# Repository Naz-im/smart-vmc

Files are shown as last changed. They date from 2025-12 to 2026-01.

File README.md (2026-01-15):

# Projet Ventilation (VMC) + App de Monitoring

## 1. Résumé du projet

Notre projet consiste à réaliser un dispositif IoT permettant d'ajuster automatiquement la ventilation (VMC) selon les conditions météo et de qualité de l’air (pluie, vent, ensoleillement, pollution, humidité si disponible) et offrant une application de monitoring et de contrôle manuel pour l'utilisateur.

## 2. Contexte et objectifs

- **Contexte** : maison connectée, qualité de l’air intérieur, efficacité énergétique
- **Objectifs principaux** :
	- Assurer une bonne qualité de l’air intérieur en adaptant le débit de ventilation aux conditions (pollution extérieure, température, humidité, vent).
	- Réduire l’humidité et évacuer l’air vicié pour prévenir moisissures et inconfort.
	- Fournir un contrôle manuel et des notifications via une application.

## 3. Périmètre

- **Matériel** :
  - moteur
  - carte ESP32
- **Logiciel**: 
		- Firmware embarqué pour l’actionneur (gestion ouverture 0–100%)
		- Application mobile pour monitoring et contrôle

## 4. Acteurs

- **Utilisateur final** : propriétaire / locataire
- **Système (embarqué)** : MCU + actionneurs
- **Application mobile** : monitoring et contrôle
- **Services tiers** : APIs météo externes

## 5. Exigences fonctionnelles 

- **01 Récupération des conditions**
	- *Description* : Le système doit pouvoir récupérer la qualité de l’air (pollution), l’humidité (si disponible), la température, la luminosité et le vent via API.
	- *Priorité* : Haute
	- *Critères d'acceptation* : Données météo reçues toutes les 10 minutes; logs des valeurs stockés localement et/ou sur cloud.

- **02 Règles d’ajustement automatique de l’ouverture**
	- *Description* : Le système ajuste automatiquement l’ouverture du clapet (et donc le débit) selon des règles configurables (ex : ouvrir davantage si pollution/CO₂/humidité > seuil, réduire sinon).
	- *Priorité* : Haute
	- *Critères d'acceptation* : Scénarios de test montrant que la règle est appliquée correctement; possibilité de forcer manuellement.

- **03 Contrôle manuel depuis l'application**
	- *Description* : L'utilisateur peut ouvrir/fermer le clapet de ventilation et régler le pourcentage d’ouverture (paliers ou valeurs) depuis l'application.
	- *Priorité* : Haute
	- *Critères d'acceptation* : Commande envoyée et état mis à jour sous 3 s; remontée d'erreur si indisponible.

- **04 Mode automatique / manuel**
	- *Description* : Basculer entre mode automatique (règles air/météo) et mode manuel.
	- *Priorité* : Moyenne
	- *Critères d'acceptation* : L'état du mode est visible et persisté.

- **05 Notifications**
	- *Description* : Recevoir notifications en cas d'événement critique (ex : surcharge/surchauffe de l’actionneur, blocage clapet, conditions extrêmes) et non critiques (ex : changement de mode, ajustement d’ouverture).
	- *Priorité* : Moyenne
	- *Critères d'acceptation* : Notification reçue sur app et log enregistrés.

- **06 Historique & Dashboard**
	- *Description* : Visualiser l'historique des états (ouvert/fermé), niveaux d’ouverture (%), mesures météo/air et interventions manuelles.
	- *Priorité* : Basse
	- *Critères d'acceptation* : Graphiques consultables.

- **07 Sécurité & protection de l’actionneur**
	- *Description* : Arrêt immédiat en cas de surintensité/surchauffe de l’actionneur; alerte en cas d’obstruction/contre‑pression détectable sur le clapet.
	- *Priorité* : Critique
	- *Critères d'acceptation* : Déclenchement de l’arrêt de sécurité sous 0.5 s lors d’une surintensité.

## 6. UI / UX

- Écrans essentiels : écran principal (ouverture ventilation: ouvert/fermé, % d’ouverture), écran historique, écran réglages (seuils air/météo), écran notifications.
- Flux : connexion --> page d'accueil --> contrôle rapide --> paramètres --> logs.

## 7. Cas d'utilisation

- En tant qu'utilisateur, je veux que l’ouverture du clapet augmente automatiquement quand la qualité de l’air est mauvaise (pollution/CO₂/humidité) ou que les conditions l’exigent.
- En tant qu'utilisateur, je veux pouvoir ouvrir/fermer le clapet et régler l’ouverture manuellement depuis l'app.

## 8. Tests & Critères d'acceptation

- Tests unitaires : firmware logique, backend endpoints.
- Tests d'intégration : envoi de télémétrie + réaction automatique.
- Tests d'acceptation utilisateur : scénarios (pluie, vent fort, obstruction) avec résultats attendus.

## Structure du projet

- `firmware/` : code embarqué pour ESP32
- `docs/` : documentation technique et utilisateur
- `Impression3DetDecoupe/` : fichiers pour impression 3D et découpe laser
- `mobile/` : code source de l'application mobile contenant principalement:
	- `android/` : code source Android pour la compilation, la génération de l'APK etc.
	- `components/` : composants réutilisables de l'application mobile
	- `hooks/` : hooks personnalisés pour la gestion de l'état et des effets secondaires
	- `App.tsx` : point d'entrée principal de l'application mobile
	- `apk/` : APK pré-généré de l'application mobile pour installation directe
	- `services/` : services pour l'application mobile (notifications, ...)
	- (Le reste des fichiers sont des configurations pour les IDE ou autres outils de développement)

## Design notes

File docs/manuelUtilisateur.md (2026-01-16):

# Manuel Utilisateur

## Installation et déploiement

Ce document décrit les procédures techniques pour flasher le microcontrôleur **ESP32** et déployer l'application mobile de monitoring.

### Flashage du Firmware sur ESP32

Le projet Le projet utilise PlatformIO pour la gestion du firmware, comme indiqué par le fichier de configuration `firmware/platformio.ini`.

#### Prérequis logiciels

- Installer [PlatformIO](https://platformio.org/install/ide?install=vscode) (extension pour VSCode recommandée).

- Avoir les drivers USB pour ESP32 installés.

#### Étapes de flashage

- Ouvrir le dossier firmware dans VSCode avec PlatformIO.
- PlatformIO détectera automatiquement le fichier `platformio.ini`.
- Connecter l'ESP32 via USB à l'ordinateur.
- Lorsque vous êtes prêt à flasher, placer vous sur le fichier `src/main.cpp` et cliquer sur l'icône "Upload" dans la barre d'outils en bas de VSCode.


- Attendre la fin du processus de compilation et de flashage. Vous verrez les logs dans la console PlatformIO.
- Pour vérifier que le firmware fonctionne, ouvrez le moniteur série en cliquant sur l'icône "Serial Monitor" dans la barre d'outils afin de voir les messages de debug.



*Note: Il est possible selon votre configuration machine que vscode n'ai pas les droits nécessaires pour accéder au port série. Dans ce cas, vous pouvez utiliser une solution immédiate mais pas très sécurisée:*

```bash
sudo chmod 666 /dev/ttyUSB0
```

*Remplacez `/dev/ttyUSB0` par le port série correspondant à votre ESP32.*

### Lancement de l'application mobile (Mode développement)

L'application mobile est développée avec React Native. Voici comment la lancer en mode développement.

#### Prérequis logiciels

- Installer [Node.js](https://nodejs.org/) version 20 ou supérieure sur votre machine.
- Installer JDK 17 pour être compatible avec gradle.
- Installer Android Studio pour émuler un appareil Android ou utiliser un appareil physique.

#### Installation des dépendances

- Ouvrir un terminal et naviguer vers le dossier `mobile`.
- Exécuter la commande suivante pour installer les dépendances :
  ```bash
  npm install
  ```

#### Lancement de l'application

Vous avez besoin de deux terminaux :

1. Dans le premier terminal, toujours dans le dossier `mobile`, lancer le serveur Metro avec la commande :
   ```bash
   npm start
   ```

2. Dans le second terminal, lancer l'application sur un émulateur ou un appareil connecté avec la commande :
   ```bash
    npm run android
    ```

*Note : Assurez-vous qu'Android Studio est lancé avec un émulateur lancé ou un téléphone Android branché avec le "Débogage USB" activé.*

L'application devrait se lancer sur l'émulateur ou l'appareil connecté. Vous pouvez maintenant interagir avec l'application mobile pour le monitoring et le contrôle de la ventilation.

#### Génération d'un APK pour distribution

Si vous souhaitez installer l'application sur un téléphone sans utiliser le mode développement (usage "client"), vous devez générer un fichier APK.

Pour des notions de praticité, un apk de l'état du projet au rendu est disponible dans le dossier `mobile/apk`

Sinon vous pouvez le générer:

1. Générer l'APK en mode release avec la commande :
   ```bash
   cd android
   ./gradlew assembleRelease
   ```
2. L'APK généré se trouvera dans le dossier `android/app/build/outputs/apk/release/`. Vous pouvez l'installer sur un appareil Android soit:
   - En le transférant via USB et en l'ouvrant sur l'appareil.
   - Avec adbr sideloading :
     ```bash
     adb install -r mobile/android/app/build/outputs/apk/release/app-release.apk
     ```

L'application devrait maintenant être installée et prête à l'emploi sur votre appareil Android.

## Utilisation de l'application

L'application mobile permet de surveiller et de contrôler le dispositif de ventilation. Voici les principales fonctionnalités :

### Première connexion

- Ouvrez l'application sur votre appareil Android.
- L'application doit tout d'abord permettre de configurer les paramètres wi-fi pour que l'ESP32 puisse se connecter à votre réseau domestique.
- Suivez les instructions à l'écran pour entrer le SSID et le mot de passe de votre réseau Wi-Fi. Vous verrer également la possibilité de configurer la latitude et la longitude pour la récupération des données météo, celle-ci sont pré-remplis selon votre position GPS si vous avez autorisé l'application à y accéder sinon par défaut sur Grenoble.

<p align="center">
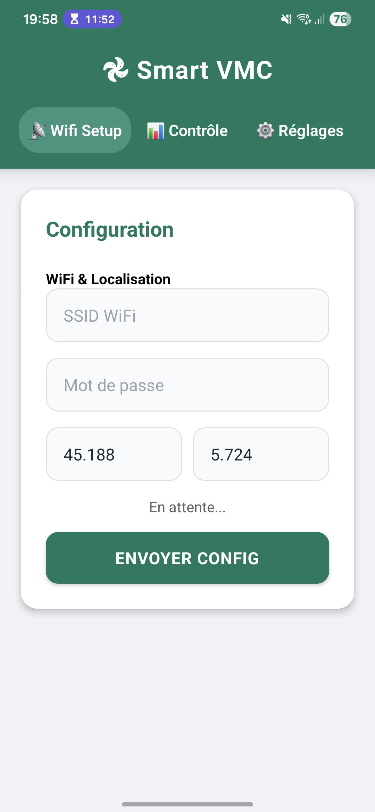
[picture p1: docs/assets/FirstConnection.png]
First Connection
    
</p>

### Dashboard principal

- Après la connexion, vous serez redirigé vers le tableau de bord principal. (Il n'est plus nécessaire de se reconnecter à chaque ouverture de l'application, les paramètres sont sauvegardés localement).
- Le tableau de bord affiche l'état actuel du clapet de ventilation (ouvert/fermé), le pourcentage d'ouverture, ainsi que les données météo et qualité de l'air en temps réel.

<p align="center">
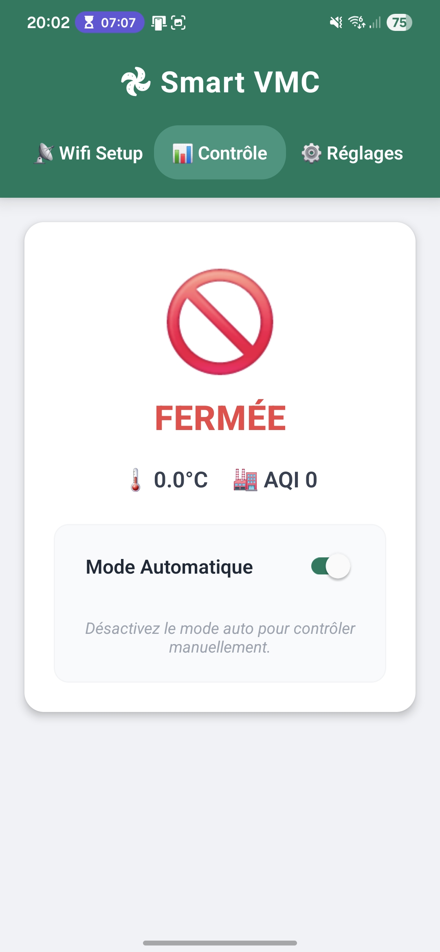
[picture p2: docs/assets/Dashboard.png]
Dashboard
    
</p>

D'ici, vous pouvez switcher entre le mode automatique et manuel, une fois en mode manuel vous pouvez régler l'ouverture du clapet via le slider ou les boutons d'ouverture/fermeture rapide.

<p align="center">
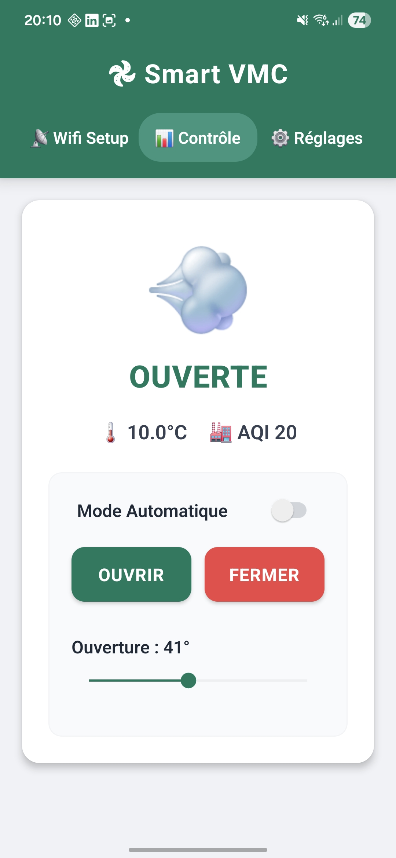
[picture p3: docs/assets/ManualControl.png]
Manual Control
    
</p>

En cas d'activation de la sécurité de blocage, un message d'alerte s'affichera:

<p align="center">
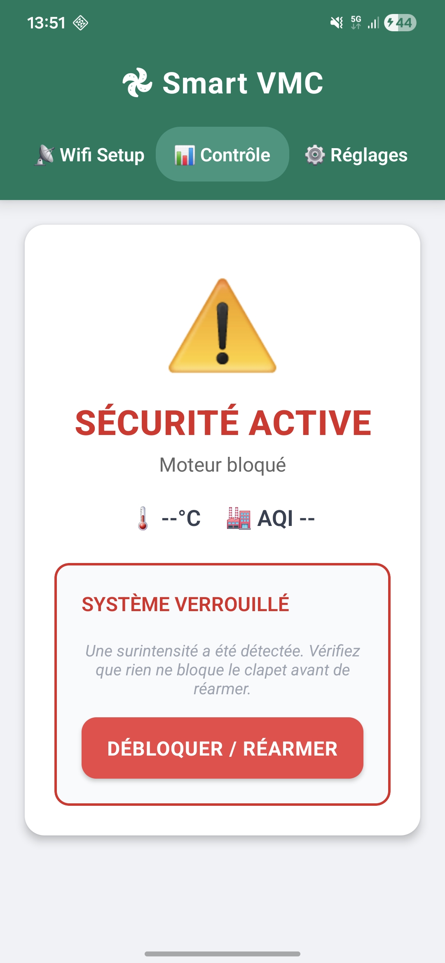
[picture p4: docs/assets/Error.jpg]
Alert
    
</p>

### Paramétrage des seuils

- Accédez à l'écran des paramètres en cliquant sur l'icône d'engrenage suivi de reglages.
- Ici, vous pouvez définir les seuils pour le mode automatique.

<p align="center">
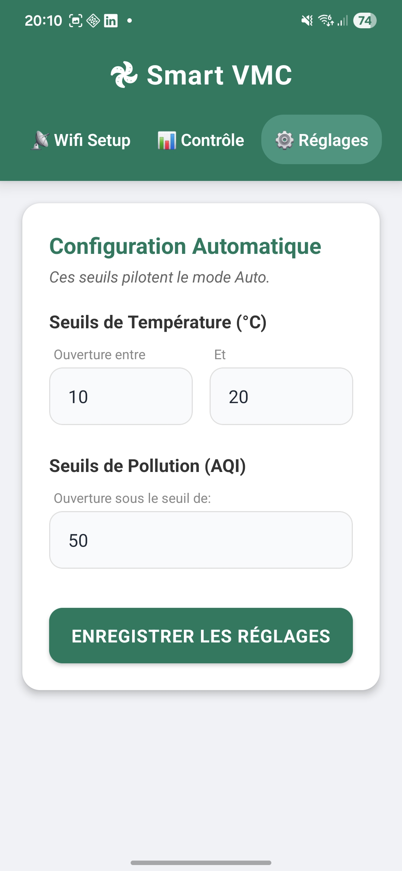
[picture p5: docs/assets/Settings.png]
Settings
    
</p>

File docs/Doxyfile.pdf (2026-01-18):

## Smart VMC

1.0

Generated on Sun Jan 18 2026 09:43:30 for Smart VMC by Doxygen 1.15.0

Sun Jan 18 2026 09:43:30

# Chapter 1

# Directory Hierarchy

## 1.1 Directories

components | | ??
dashboard | | ??
ControlPanel.tsx | | ??
SensorRow.tsx | | ??
StatusDisplay.tsx | ??
ui | ??
AppButton.tsx | ??
AppInput.tsx | ??
Card.tsx | ??
ConfigurationPanel.tsx | ??
DashboardPanel.tsx | ??
SetupPanel.tsx | ??
TabHeader.tsx | ??
dashboard | | | ??
ControlPanel.tsx | | ??
SensorRow.tsx | | ??
StatusDisplay.tsx | ??
firmware | ??
src | ??
main.hpp | | ??
hooks | | ??
useBLE.ts | ??
useWindowApi.ts | ??
mobile | ??
components | ??
dashboard | | ??
ControlPanel.tsx | | ??
SensorRow.tsx | | ??
StatusDisplay.tsx | ??
ui | ??
AppButton.tsx | ??
AppInput.tsx | ??
Card.tsx | ??
ConfigurationPanel.tsx | ??
DashboardPanel.tsx | ??
SetupPanel.tsx | ??

Generated on Sun Jan 18 2026 09:43:30 for Smart VMC by Doxygen

### 2 Directory Hierarchy

TabHeader.tsx | ??
hooks | ??
useBLE.ts | ??
useWindowApi.ts | ??
services | ??
NotificationService.ts | ??
App.tsx | | ??
services | | ??
NotificationService.ts | ??
src | | ??
main.hpp | | ??
ui | | | ??
AppButton.tsx | ??
AppInput.tsx | ??
Card.tsx | ??

# Chapter 2

# Hierarchical Index

## 2.1 Class Hierarchy

This inheritance list is sorted roughly, but not completely, alphabetically:

AppButtonProps | | | ??
BLECharacteristicCallbacks
ConfigCallbacks | ??
CardProps | | | ??
ConfigurationPanelProps | | ??
ControlPanelProps | | ??
DashboardPanelProps | | ??
NotificationService | | | ??
SensorRowProps | | ??
SetupPanelProps | | ??
StatusDisplayProps | | ??
TabHeaderProps | | | ??
TextInputProps
AppInputProps | | ??
WindowState | | ??

### 4 Hierarchical Index

# Chapter 3

# Class Index

## 3.1 Class List

Here are the classes, structs, unions and interfaces with brief descriptions:

AppButtonProps
Propriétés du bouton | ??
AppInputProps
Propriétés du champ de saisie | ??
CardProps
Propriétés du composant carte | ??
ConfigCallbacks
Traite les configurations WiFi et de localisation | ??
ConfigurationPanelProps
Propriétés du panneau de configuration | ??
ControlPanelProps
Propriétés du panneau de contrôle | ??
DashboardPanelProps
Propriétés du tableau de bord | | | ??
NotificationService
Service pour gérer les notifications locales | ??
SensorRowProps
Propriétés de la ligne de capteurs | | | ??
SetupPanelProps
Propriétés du panneau de configuration initiale | | | ??
StatusDisplayProps
Propriétés de l'affichage d'état | ??
TabHeaderProps
Propriétés de l’en-tête d’onglets | | | ??
WindowState
État de la fenêtre côté mobile | ??

### 6 Class Index

# Chapter 4

# File Index

## 4.1 File List

Here is a list of all files with brief descriptions:

firmware/src/main.hpp
Déclarations principales pour le firmware de contrôle de fenêtre VMC | | | ??
mobile/App.tsx
Composant principal de l'application mobile Smart VMC | | | ??
mobile/components/ConfigurationPanel.tsx
Panneau de configuration des seuils de température et pollution | | | ??
mobile/components/DashboardPanel.tsx
Tableau de bord affichant l’état, les capteurs et les commandes de la VMC | ??
mobile/components/SetupPanel.tsx
Panneau de configuration initiale avec saisie WiFi et localisation | | | ??
mobile/components/TabHeader.tsx
Barre d’onglets principale | ??
mobile/components/dashboard/ControlPanel.tsx
Panneau de contrôle de la VMC (mode auto, commandes manuelles, slider) | ??
mobile/components/dashboard/SensorRow.tsx
Ligne d'affichage des valeurs de capteurs (température et AQI) | ??
mobile/components/dashboard/StatusDisplay.tsx
Affichage de l'état global de la VMC (ouverte/fermée/verrouillée) | ??
mobile/components/ui/AppButton.tsx
Bouton applicatif stylé (primaire, danger, outline) avec état de chargement | ??
mobile/components/ui/AppInput.tsx
Champ de saisie stylé avec placeholder grisé | ??
mobile/components/ui/Card.tsx
Conteneur carte avec ombre et arrondis | ??
mobile/hooks/useBLE.ts
Hook React pour la communication Bluetooth avec l'ESP32 | ??
mobile/hooks/useWindowApi.ts
Hook React pour communiquer avec l'API smart-vmc | | ??
mobile/services/NotificationService.ts | | | ??

### 8 File Index

# Chapter 5

# Directory Documentation

## 5.1 mobile/components Directory Reference

Directories

- directory dashboard
- directory ui

Files

- file ConfigurationPanel.tsx

Panneau de configuration des seuils de température et pollution.
- file DashboardPanel.tsx

Tableau de bord affichant l’état, les capteurs et les commandes de la VMC.
- file SetupPanel.tsx

Panneau de configuration initiale avec saisie WiFi et localisation.
- file TabHeader.tsx

Barre d’onglets principale.

## 5.2 mobile/components/dashboard Directory Reference

Files

- file ControlPanel.tsx

Panneau de contrôle de la VMC (mode auto, commandes manuelles, slider).
- file SensorRow.tsx

Ligne d'affichage des valeurs de capteurs (température et AQI).
- file StatusDisplay.tsx

Affichage de l'état global de la VMC (ouverte/fermée/verrouillée).

## 5.3 firmware Directory Reference

Directories

- directory src

### 10 Directory Documentation

## 5.4 mobile/hooks Directory Reference

Files

- file useBLE.ts

Hook React pour la communication Bluetooth avec l'ESP32.
- file useWindowApi.ts

Hook React pour communiquer avec l'API smart-vmc.

## 5.5 mobile Directory Reference

Directories

- directory components
- directory hooks
- directory services

Files

- file App.tsx

Composant principal de l'application mobile Smart VMC.

## 5.6 mobile/services Directory Reference

Files

- file NotificationService.ts

## 5.7 firmware/src Directory Reference

Files

- file main.hpp

Déclarations principales pour le firmware de contrôle de fenêtre VMC.

## 5.8 mobile/components/ui Directory Reference

Files

- file AppButton.tsx

Bouton applicatif stylé (primaire, danger, outline) avec état de chargement.
- file AppInput.tsx

Champ de saisie stylé avec placeholder grisé
- file Card.tsx

Conteneur carte avec ombre et arrondis.

# Chapter 6

# Class Documentation

## 6.1 AppButtonProps Interface Reference

Propriétés du bouton.

### 6.1.1 Detailed Description

Propriétés du bouton.

The documentation for this interface was generated from the following file:

- mobile/components/ui/AppButton.tsx

## 6.2 AppInputProps Interface Reference

Propriétés du champ de saisie.

Inheritance diagram for AppInputProps:

AppInputProps

TextInputProps

### 6.2.1 Detailed Description

Propriétés du champ de saisie.

The documentation for this interface was generated from the following file:

- mobile/components/ui/AppInput.tsx

### 12 Class Documentation

## 6.3 CardProps Interface Reference

Propriétés du composant carte.

### 6.3.1 Detailed Description

Propriétés du composant carte.

The documentation for this interface was generated from the following file:

- mobile/components/ui/Card.tsx

## 6.4 ConfigCallbacks Class Reference

Traite les configurations WiFi et de localisation.

#include <main.hpp>

Inheritance diagram for ConfigCallbacks:

ConfigCallbacks

BLECharacteristicCallbacks

### 6.4.1 Detailed Description

Traite les configurations WiFi et de localisation.

The documentation for this class was generated from the following file:

- firmware/src/main.hpp

## 6.5 ConfigurationPanelProps Interface Reference

Propriétés du panneau de configuration.

### 6.5.1 Detailed Description

Propriétés du panneau de configuration.

The documentation for this interface was generated from the following file:

- mobile/components/ConfigurationPanel.tsx

6.6 ControlPanelProps Interface Reference | 13

## 6.6 ControlPanelProps Interface Reference

Propriétés du panneau de contrôle.

### 6.6.1 Detailed Description

Propriétés du panneau de contrôle.

The documentation for this interface was generated from the following file:

- mobile/components/dashboard/ControlPanel.tsx

## 6.7 DashboardPanelProps Interface Reference

Propriétés du tableau de bord.

### 6.7.1 Detailed Description

Propriétés du tableau de bord.

The documentation for this interface was generated from the following file:

- mobile/components/DashboardPanel.tsx

## 6.8 NotificationService Class Reference

Service pour gérer les notifications locales.

Public Member Functions

- async requestPermission ()

@function requestPermission
- async createChannel ()

@function createChannel
- async displayNotification (title:string, body:string)

@function displayNotification

### 6.8.1 Detailed Description

Service pour gérer les notifications locales.

Ce service utilise la bibliothèque Notifee pour :

- Demander la permission d'envoyer des notifications
- Créer un canal de notification pour les alertes VMC
- Afficher des notifications locales avec un titre et un corps

### 14 Class Documentation

### 6.8.2 Member Function Documentation

### 6.8.2.1 createChannel()

async NotificationService::createChannel () [inline]

@function createChannel

Crée un canal de notification pour les alertes VMC

Returns

{Promise<string>} L'ID du canal créé

### 6.8.2.2 displayNotification()

async NotificationService::displayNotification (

title:string,

body:string) [inline]

@function displayNotification

Affiche une notification locale avec le titre et le corps spécifiés

Parameters

{string} | title - Le titre de la notification
{string} | body - Le corps de la notification

### 6.8.2.3 requestPermission()

async NotificationService::requestPermission () [inline]

@function requestPermission

Demande la permission d'envoyer des notifications

Returns

{Promise<boolean>} Vrai si la permission est accordée, sinon faux

The documentation for this class was generated from the following file:

- mobile/services/NotificationService.ts

## 6.9 SensorRowProps Interface Reference

Propriétés de la ligne de capteurs.

6.10 SetupPanelProps Interface Reference | 15

### 6.9.1 Detailed Description

Propriétés de la ligne de capteurs.

The documentation for this interface was generated from the following file:

- mobile/components/dashboard/SensorRow.tsx

## 6.10 SetupPanelProps Interface Reference

Propriétés du panneau de configuration initiale.

### 6.10.1 Detailed Description

Propriétés du panneau de configuration initiale.

The documentation for this interface was generated from the following file:

- mobile/components/SetupPanel.tsx

## 6.11 StatusDisplayProps Interface Reference

Propriétés de l'affichage d'état.

### 6.11.1 Detailed Description

Propriétés de l'affichage d'état.

The documentation for this interface was generated from the following file:

- mobile/components/dashboard/StatusDisplay.tsx

## 6.12 TabHeaderProps Interface Reference

Propriétés de l’en-tête d’onglets.

### 6.12.1 Detailed Description

Propriétés de l’en-tête d’onglets.

The documentation for this interface was generated from the following file:

- mobile/components/TabHeader.tsx

### 16 Class Documentation

## 6.13 WindowState Interface Reference

État de la fenêtre côté mobile.

### 6.13.1 Detailed Description

État de la fenêtre côté mobile.

The documentation for this interface was generated from the following file:

- mobile/hooks/useWindowApi.ts

# Chapter 7

# File Documentation

## 7.1 firmware/src/main.hpp File Reference

Déclarations principales pour le firmware de contrôle de fenêtre VMC.

#include <Arduino.h>

#include <WiFi.h>

#include <HTTPClient.h>

#include <WebServer.h>

#include <ArduinoJson.h>

#include <ESP32Servo.h>

#include <NimBLEDevice.h>

#include <Preferences.h>

Classes

- class ConfigCallbacks

Traite les configurations WiFi et de localisation.

Macros

- #define SERVO_PIN 13

Variable pin du servomoteur.
- #define CURRENT_SENSOR_PIN 34

Variable pin du capteur de courant.
- #define MAX_CURRENT_THRESHOLD 2500

Seuil de courant maximal en mA.
- #define SERVICE_UUID "4fafc201-1fb5-459e-8fcc-c5c9c331914b"

UUIDs pour le service et les caractéristiques BLE.
- #define CHAR_CONFIG_UUID "beb5483e-36e1-4688-b7f5-ea07361b26a8"

UUID de la caractéristique de configuration (WiFi, localisation).
- #define CHAR_IP_UUID "12345678-1234-1234-1234-1234567890ab"

UUID de la caractéristique d'adresse IP.

### 18 File Documentation

Functions

- bool checkSafety ()

Vérifie l'état de sécurité du système.
- void setVMC (int angle)

Commande le servomoteur à un angle spécifique.
- void handleStatus ()

Gestionnaire HTTP GET /api/window/status.
- void handleControl ()

Gestionnaire HTTP POST /api/window/control.
- void setup ()

Initialisation de la connexion (WiFi, BLE, serveur).
- void loop ()

Boucle d'exécution principale.

Variables

- Servo windowServo

Objet servomoteur pour contrôler l'ouverture de la fenêtre.
- Preferences preferences

Objet Preferences pour stocker la configuration persistante.
- WebServer server

Objet WebServer pour gérer les requêtes HTTP.
- BLECharacteristic ∗ pIpChar

Caractéristique BLE pour l'adresse IP.
- String wifi_ssid

SSID WiFi.
- String wifi_pass

Mot de passe WiFi.
- float latitude

Variable de configuration de localisation.
- float longitude

Variable de configuration de localisation.
- float tempMax

Variables de configuration de la température maximum.
- float tempMin

Variables de configuration de la température minimum.
- int aqiMax

Variables de configuration de la qualité de l'air maximum.
- bool isOpen

Indique si la ventilation est ouverte.
- bool autoMode

Indique si le mode automatique est activé
- int targetAngle

Angle cible pour le servomoteur.
- bool safetyLockout

Indique si le verrouillage de sécurité est activé
- int lastCurrentReading

Dernière lecture du courant en mA.
- int currentAngle

7.1 firmware/src/main.hpp File Reference | 19

Angle actuel du servomoteur.
- float lastTemp

Dernière température lue.
- int lastAQI

Dernière qualité de l'air lue.
- unsigned long lastWeatherCheck

Timestamp de la dernière vérification météo.
- bool shouldRestart

Indique si un redémarrage est nécessaire.

### 7.1.1 Detailed Description

Déclarations principales pour le firmware de contrôle de fenêtre VMC.

### 7.1.2 Macro Definition Documentation

### 7.1.2.1 CHAR_CONFIG_UUID

#define CHAR_CONFIG_UUID "beb5483e-36e1-4688-b7f5-ea07361b26a8"

UUID de la caractéristique de configuration (WiFi, localisation).

### 7.1.2.2 CHAR_IP_UUID

#define CHAR_IP_UUID "12345678-1234-1234-1234-1234567890ab"

UUID de la caractéristique d'adresse IP.

### 7.1.2.3 CURRENT_SENSOR_PIN

#define CURRENT_SENSOR_PIN 34

Variable pin du capteur de courant.

### 7.1.2.4 MAX_CURRENT_THRESHOLD

#define MAX_CURRENT_THRESHOLD 2500

Seuil de courant maximal en mA.

### 7.1.2.5 SERVICE_UUID

#define SERVICE_UUID "4fafc201-1fb5-459e-8fcc-c5c9c331914b"

UUIDs pour le service et les caractéristiques BLE.

### 20 File Documentation

### 7.1.2.6 SERVO_PIN

#define SERVO_PIN 13

Variable pin du servomoteur.

### 7.1.3 Function Documentation

### 7.1.3.1 checkSafety()

bool checkSafety ()

Vérifie l'état de sécurité du système.

Lit le capteur de courant et vérifie s'il dépasse le seuil

Returns

true si sécurisé, false si surintensité détectée

### 7.1.3.2 handleControl()

void handleControl ()

Gestionnaire HTTP POST /api/window/control.

Reçoit les commandes pour contrôler la fenêtre

### 7.1.3.3 handleStatus()

void handleStatus ()

Gestionnaire HTTP GET /api/window/status.

Retourne l'état complet du système en JSON

### 7.1.3.4 loop()

void loop ()

Boucle d'exécution principale.

Gère les requêtes HTTP, la météo et les redémarrages

### 7.1.3.5 setup()

void setup ()

Initialisation de la connexion (WiFi, BLE, serveur).

### 7.1.3.6 setVMC()

void setVMC (

int angle)

Commande le servomoteur à un angle spécifique.

Parameters

7.1 firmware/src/main.hpp File Reference | 21
angle | Angle cible en degrés (0-90)

Vérifie la sécurité, contraint l'angle et met à jour l'état

### 7.1.4 Variable Documentation

### 7.1.4.1 aqiMax

int aqiMax [extern]

Variables de configuration de la qualité de l'air maximum.

### 7.1.4.2 autoMode

bool autoMode [extern]

Indique si le mode automatique est activé

### 7.1.4.3 currentAngle

int currentAngle [extern]

Angle actuel du servomoteur.

### 7.1.4.4 isOpen

bool isOpen [extern]

Indique si la ventilation est ouverte.

### 7.1.4.5 lastAQI

int lastAQI [extern]

Dernière qualité de l'air lue.

### 7.1.4.6 lastCurrentReading

int lastCurrentReading [extern]

Dernière lecture du courant en mA.

### 22 File Documentation

### 7.1.4.7 lastTemp

float lastTemp [extern]

Dernière température lue.

### 7.1.4.8 lastWeatherCheck

unsigned long lastWeatherCheck [extern]

Timestamp de la dernière vérification météo.

### 7.1.4.9 latitude

float latitude [extern]

Variable de configuration de localisation.

### 7.1.4.10 longitude

float longitude [extern]

Variable de configuration de localisation.

### 7.1.4.11 pIpChar

BLECharacteristic∗ pIpChar [extern]

Caractéristique BLE pour l'adresse IP.

### 7.1.4.12 preferences

Preferences preferences [extern]

Objet Preferences pour stocker la configuration persistante.

### 7.1.4.13 safetyLockout

bool safetyLockout [extern]

Indique si le verrouillage de sécurité est activé

### 7.1.4.14 server

WebServer server [extern]

Objet WebServer pour gérer les requêtes HTTP.

7.1 firmware/src/main.hpp File Reference | 23

### 7.1.4.15 shouldRestart

bool shouldRestart [extern]

Indique si un redémarrage est nécessaire.

### 7.1.4.16 targetAngle

int targetAngle [extern]

Angle cible pour le servomoteur.

### 7.1.4.17 tempMax

float tempMax [extern]

Variables de configuration de la température maximum.

### 7.1.4.18 tempMin

float tempMin [extern]

Variables de configuration de la température minimum.

### 7.1.4.19 wifi_pass

String wifi_pass [extern]

Mot de passe WiFi.

### 7.1.4.20 wifi_ssid

String wifi_ssid [extern]

SSID WiFi.

### 7.1.4.21 windowServo

Servo windowServo [extern]

Objet servomoteur pour contrôler l'ouverture de la fenêtre.

### 24 File Documentation

## 7.2 main.hpp

Go to the documentation of this file.

00001 #ifndef MAIN_HPP
00002 #define MAIN_HPP
00003
00004 #include <Arduino.h> 00005 #include <WiFi.h>
00006 #include <HTTPClient.h> 00007 #include <WebServer.h> 00008 #include <ArduinoJson.h> 00009 #include <ESP32Servo.h> 00010 #include <NimBLEDevice.h> 00011 #include <Preferences.h> 00012
00016
00020 #define SERVO_PIN 13
00024 #define CURRENT_SENSOR_PIN 34
00028 #define MAX_CURRENT_THRESHOLD 2500
00032 #define SERVICE_UUID "4fafc201-1fb5-459e-8fcc-c5c9c331914b" 00036 #define CHAR_CONFIG_UUID "beb5483e-36e1-4688-b7f5-ea07361b26a8" 00040 #define CHAR_IP_UUID "12345678-1234-1234-1234-1234567890ab" 00041
00045 extern Servo windowServo;
00046
00050 extern Preferences preferences; 00051
00055 extern WebServer server;
00056
00060 extern BLECharacteristic *pIpChar; 00061
00065 extern String wifi_ssid;
00069 extern String wifi_pass;
00070
00074 extern float latitude; 00078 extern float longitude; 00082 extern float tempMax; 00086 extern float tempMin; 00090 extern int aqiMax;
00091
00095 extern bool isOpen;
00096
00100 extern bool autoMode;
00104 extern int targetAngle;
00108 extern bool safetyLockout; 00112 extern int lastCurrentReading; 00116 extern int currentAngle;
00120 extern float lastTemp;
00124 extern int lastAQI;
00128 extern unsigned long lastWeatherCheck; 00132 extern bool shouldRestart;
00133
00139 bool checkSafety();
00140
00146 void setVMC(int angle); 00147
00152 void handleStatus(); 00153
00158 void handleControl(); 00159
00163 void setup();
00168 void loop();
00169
00171
00176 class ConfigCallbacks : public BLECharacteristicCallbacks {
00181 | void onWrite(BLECharacteristic *pCharacteristic);
00182 };
00183
00184 #endif // MAIN_HPP

## 7.3 mobile/App.tsx File Reference

Composant principal de l'application mobile Smart VMC.

7.3 mobile/App.tsx File Reference | 25

Variables

- import React
- import import { SafeAreaView, ScrollView, StatusBar, StyleSheet, Alert, ActivityIndicator, View, Text } from 'react-native'
- import AsyncStorage from react native async storage async storage
- import TabHeader from components TabHeader
- import SetupPanel from components SetupPanel
- import DashboardPanel from components DashboardPanel
- import ConfigurationPanel from components ConfigurationPanel
- function App() export default App

@function App

### 7.3.1 Detailed Description

Composant principal de l'application mobile Smart VMC.

Gère la navigation entre les onglets (Setup, Dashboard, Configuration) et la communication avec l'ESP32 via BLE et API HTTP

### 7.3.2 Variable Documentation

### 7.3.2.1 App

function App () export default App ()

@function App

Composant racine de l'application Smart VMC

Gère :

- La navigation entre 3 onglets (Setup, Dashboard, Configuration)
- La connexion BLE à l'ESP32
- La communication avec l'API REST
- Le stockage persistant de l'adresse IP du serveur

Returns

{React.JSX.Element} Interface utilisateur complète

### 7.3.2.2 ConfigurationPanel

export default ConfigurationPanel

### 26 File Documentation

### 7.3.2.3 DashboardPanel

export default DashboardPanel

### 7.3.2.4 import

import { SafeAreaView, ScrollView, StatusBar, StyleSheet, Alert, ActivityIndicator, View, Text

} from 'react-native'

### 7.3.2.5 React

import React

### 7.3.2.6 SetupPanel

export default SetupPanel

### 7.3.2.7 storage

import AsyncStorage from react native async storage async storage

### 7.3.2.8 TabHeader

export default TabHeader

## 7.4 mobile/components/ConfigurationPanel.tsx File Reference

Panneau de configuration des seuils de température et pollution.

Variables

- import React
- import import { View, Text, StyleSheet, Alert } from 'react-native'
- onUpdateThresholds __pad0__
- onUpdateThresholds tMin
- onUpdateThresholds aqiMax

Variables de configuration de la qualité de l'air maximum.
- isLoading __pad1__
- const ConfigurationPanel

@function ConfigurationPanel
- const onUpdateThresholds
- const isLoading
- const styles

7.4 mobile/components/ConfigurationPanel.tsx File Reference | 27

### 7.4.1 Detailed Description

Panneau de configuration des seuils de température et pollution.

### 7.4.2 Variable Documentation

### 7.4.2.1 __pad0__

onUpdateThresholds __pad0__

### 7.4.2.2 __pad1__

isLoading __pad1__

### 7.4.2.3 aqiMax

onUpdateThresholds aqiMax

Variables de configuration de la qualité de l'air maximum.

### 7.4.2.4 ConfigurationPanel

export default ConfigurationPanel

@function ConfigurationPanel

Formulaire de configuration des seuils (température, AQI) pour le mode Auto

Parameters

{ConfigurationPanelProps} props - Propriétés du composant

Returns

{React.JSX.Element} Carte de configuration

### 7.4.2.5 import

import { View, Text, StyleSheet, Alert } from 'react-native'

### 7.4.2.6 isLoading

const isLoading

### 28 File Documentation

### 7.4.2.7 onUpdateThresholds

const onUpdateThresholds

### 7.4.2.8 React

import React

### 7.4.2.9 styles

const styles

### 7.4.2.10 tMin

onUpdateThresholds tMin

## 7.5 mobile/components/dashboard/ControlPanel.tsx File Reference

Panneau de contrôle de la VMC (mode auto, commandes manuelles, slider).

Variables

- import React from react
- import { View, Text, Switch, StyleSheet } from 'react-native'
- import Slider from react native community slider
- isLocked __pad0__
- targetAngle __pad1__
- onToggleAuto __pad2__
- onCommand __pad3__
- onAngleChange __pad4__
- onResetSafety __pad5__
- export const ControlPanel

@function ControlPanel
- export const isLocked
- export const targetAngle

Angle cible pour le servomoteur.
- export const onToggleAuto
- export const onCommand
- export const onAngleChange
- export const onResetSafety
- const styles

### 7.5.1 Detailed Description

Panneau de contrôle de la VMC (mode auto, commandes manuelles, slider).

7.5 mobile/components/dashboard/ControlPanel.tsx File Reference | 29

### 7.5.2 Variable Documentation

### 7.5.2.1 __pad0__

isLocked __pad0__

### 7.5.2.2 __pad1__

targetAngle __pad1__

### 7.5.2.3 __pad2__

onToggleAuto __pad2__

### 7.5.2.4 __pad3__

onCommand __pad3__

### 7.5.2.5 __pad4__

onAngleChange __pad4__

### 7.5.2.6 __pad5__

onResetSafety __pad5__

### 7.5.2.7 ControlPanel

export const ControlPanel

@function ControlPanel

Panneau de contrôle principal de la VMC

Parameters

{ControlPanelProps} props - Propriétés du composant

Returns

{React.JSX.Element} Panneau de contrôle

Affiche deux modes :

- Mode verrouillé : Bouton de réarmement sécurité
- Mode normal : Switch auto/manuel, boutons ouvrir/fermer, slider d'angle

### 30 File Documentation

### 7.5.2.8 import

import { View, Text, Switch, StyleSheet } from 'react-native'

### 7.5.2.9 isLocked

export const isLocked

### 7.5.2.10 onAngleChange

export const onAngleChange

### 7.5.2.11 onCommand

export const onCommand

### 7.5.2.12 onResetSafety

export const onResetSafety

### 7.5.2.13 onToggleAuto

export const onToggleAuto

### 7.5.2.14 react

import React from react

### 7.5.2.15 slider

import Slider from react native community slider

### 7.5.2.16 styles

const styles

### 7.5.2.17 targetAngle

export const targetAngle

Angle cible pour le servomoteur.

7.6 mobile/components/dashboard/SensorRow.tsx File Reference | 31

## 7.6 mobile/components/dashboard/SensorRow.tsx File Reference

Ligne d'affichage des valeurs de capteurs (température et AQI).

Variables

- import React from react
- import { View, Text, StyleSheet } from 'react-native'
- aqi __pad0__
- export const SensorRow

@function SensorRow
- export const aqi
- const styles

### 7.6.1 Detailed Description

Ligne d'affichage des valeurs de capteurs (température et AQI).

### 7.6.2 Variable Documentation

### 7.6.2.1 __pad0__

aqi __pad0__

### 7.6.2.2 aqi

export const aqi

Initial value:

=> {
return (
<View style={styles.row}>
<Text style={styles.value}> {temp !== undefined && temp !== null ? temp.toFixed(1) : ’--’}°C</Text> <Text style={styles.value}> AQI {aqi ?? ’--’}</Text>
</View>
);
}

### 7.6.2.3 import

import { View, Text, StyleSheet } from 'react-native'

### 7.6.2.4 react

import React from react

### 7.6.2.5 SensorRow

export const SensorRow

@function SensorRow

Affiche la température et l'AQI sous forme de badges

Parameters

### 32 File Documentation

{SensorRowProps} props - Propriétés du composant

Returns

{React.JSX.Element} Ligne de capteurs

### 7.6.2.6 styles

const styles

Initial value:

= StyleSheet.create({
row: {
flexDirection: ’row’,
justifyContent: ’center’,
gap: 20,
marginBottom: 25,
},
value: {
fontSize: 18,
fontWeight: ’600’,
color: ’#374151’,
},
})

## 7.7 mobile/components/dashboard/StatusDisplay.tsx File Reference

Affichage de l'état global de la VMC (ouverte/fermée/verrouillée).

Variables

- import React from react
- import { View, Text, StyleSheet } from 'react-native'
- isLocked __pad0__
- export const StatusDisplay

@function StatusDisplay
- export const isLocked
- const styles

### 7.7.1 Detailed Description

Affichage de l'état global de la VMC (ouverte/fermée/verrouillée).

### 7.7.2 Variable Documentation

### 7.7.2.1 __pad0__

isLocked __pad0__

7.7 mobile/components/dashboard/StatusDisplay.tsx File Reference | 33

### 7.7.2.2 import

import { View, Text, StyleSheet } from 'react-native'

### 7.7.2.3 isLocked

export const isLocked

Initial value:

=> {

if (isLocked) {
return (
<View style={styles.container}>
<Text style={styles.emoji}></Text>
<Text style={[styles.text, { color: ’#DC2626’ }]}> SÉCURITÉ ACTIVE
</Text>
<Text style={styles.subtext}>Moteur bloqué</Text> </View>
);
}

return (
<View style={styles.container}> <Text style={styles.emoji}> {isOpen ? ’’ : ’’}
</Text>
<Text style={[
styles.text,
{ color: isOpen ? ’#007A5E’ : ’#EF4444’ } ]}>
{isOpen ? ’OUVERTE’ : ’FERMÉE’}
</Text>
</View>
);
}

### 7.7.2.4 react

import React from react

### 7.7.2.5 StatusDisplay

export const StatusDisplay

@function StatusDisplay

Affiche l'état visuel de la VMC avec emoji et texte coloré

Parameters

{StatusDisplayProps} props - Propriétés du composant

Returns

{React.JSX.Element} Vue d'état

### 34 File Documentation

### 7.7.2.6 styles

const styles

Initial value:

= StyleSheet.create({
container: {
alignItems: ’center’,
marginBottom: 20,
},
emoji: {
fontSize: 80,
marginBottom: 10,
},
text: {
fontSize: 28,
fontWeight: ’800’,
letterSpacing: 0.5,
textAlign: ’center’,
},
subtext: {
fontSize: 16,
color: ’#666’,
marginTop: 5,
}
})

## 7.8 mobile/components/DashboardPanel.tsx File Reference

Tableau de bord affichant l’état, les capteurs et les commandes de la VMC.

Variables

- import React
- import import { StyleSheet, View } from 'react-native'
- import NotificationService from services NotificationService
- onToggleAuto __pad0__
- onCommand __pad1__
- onAngleChange __pad2__
- onResetSafety __pad3__
- const DashboardPanel

@function DashboardPanel
- const onToggleAuto
- const onCommand
- const onAngleChange
- const onResetSafety
- const styles

### 7.8.1 Detailed Description

Tableau de bord affichant l’état, les capteurs et les commandes de la VMC.

### 7.8.2 Variable Documentation

### 7.8.2.1 __pad0__

onToggleAuto __pad0__

7.8 mobile/components/DashboardPanel.tsx File Reference | 35

### 7.8.2.2 __pad1__

onCommand __pad1__

### 7.8.2.3 __pad2__

onAngleChange __pad2__

### 7.8.2.4 __pad3__

onResetSafety __pad3__

### 7.8.2.5 DashboardPanel

export default DashboardPanel

@function DashboardPanel

Affiche l’état, les capteurs et les commandes de la VMC

Parameters

{DashboardPanelProps} props - Propriétés du composant

Returns

{React.JSX.Element} Vue tableau de bord

### 7.8.2.6 import

import { StyleSheet, View } from 'react-native'

### 7.8.2.7 NotificationService

import NotificationService from services NotificationService

### 7.8.2.8 onAngleChange

const onAngleChange

### 7.8.2.9 onCommand

const onCommand

### 36 File Documentation

### 7.8.2.10 onResetSafety

const onResetSafety

### 7.8.2.11 onToggleAuto

const onToggleAuto

### 7.8.2.12 React

import React

### 7.8.2.13 styles

const styles

Initial value:

= StyleSheet.create({
container: {
alignItems: ’center’,
},
})

## 7.9 mobile/components/SetupPanel.tsx File Reference

Panneau de configuration initiale avec saisie WiFi et localisation.

Variables

- import React
- import import { View, Text, StyleSheet, Platform, Alert } from 'react-native'
- import Geolocation from react native geolocation service
- isScanning __pad0__
- onConnect __pad1__
- onConnect pass
- onConnect lat
- onConnect lon
- onConnect ip
- savedIp __pad2__
- const SetupPanel

@function SetupPanel
- const isScanning
- const onConnect
- const savedIp
- const styles

7.9 mobile/components/SetupPanel.tsx File Reference | 37

### 7.9.1 Detailed Description

Panneau de configuration initiale avec saisie WiFi et localisation.

### 7.9.2 Variable Documentation

### 7.9.2.1 __pad0__

isScanning __pad0__

### 7.9.2.2 __pad1__

onConnect __pad1__

### 7.9.2.3 __pad2__

savedIp __pad2__

### 7.9.2.4 import

import { View, Text, StyleSheet, Platform, Alert } from 'react-native'

### 7.9.2.5 ip

onConnect ip

### 7.9.2.6 isScanning

const isScanning

### 7.9.2.7 lat

onConnect lat

### 7.9.2.8 lon

onConnect lon

### 7.9.2.9 onConnect

const onConnect

### 38 File Documentation

### 7.9.2.10 pass

onConnect pass

### 7.9.2.11 React

import React

### 7.9.2.12 savedIp

const savedIp

### 7.9.2.13 service

import Geolocation from react native geolocation service

### 7.9.2.14 SetupPanel

export default SetupPanel

@function SetupPanel

Formulaire d’envoi des identifiants WiFi + localisation via BLE

Parameters

{SetupPanelProps} props - Propriétés du composant

Returns

{React.JSX.Element} Carte de configuration initiale

### 7.9.2.15 styles

const styles

Initial value:

= StyleSheet.create({
sectionTitle: { fontSize: 20, fontWeight: ’700’, marginBottom: 15, color: ’#007A5E’ }, statusText: { marginBottom: 15, textAlign: ’center’, color: ’#666’, fontSize: 14 }, })

## 7.10 mobile/components/TabHeader.tsx File Reference

Barre d’onglets principale.

7.10 mobile/components/TabHeader.tsx File Reference | 39

Variables

- import React from react
- import { View, Text, TouchableOpacity, StyleSheet } from 'react-native'
- onTabChange __pad0__
- const TabHeader

@function TabHeader
- const onTabChange
- const styles

### 7.10.1 Detailed Description

Barre d’onglets principale.

### 7.10.2 Variable Documentation

### 7.10.2.1 __pad0__

onTabChange __pad0__

### 7.10.2.2 import

import { View, Text, TouchableOpacity, StyleSheet } from 'react-native'

### 7.10.2.3 onTabChange

const onTabChange

Initial value:

=> {
return (
<View style={styles.header}>
<Text style={styles.headerTitle}> Smart VMC</Text> <View style={styles.tabs}>
<TouchableOpacity
onPress={() => onTabChange(’SETUP’)}
style={[styles.tab, activeTab === ’SETUP’ && styles.activeTab]} >
<Text style={styles.tabText}> Wifi Setup</Text> </TouchableOpacity>
<TouchableOpacity
onPress={() => onTabChange(’DASHBOARD’)}
style={[styles.tab, activeTab === ’DASHBOARD’ && styles.activeTab]} >
<Text style={styles.tabText}> Contrôle</Text>
</TouchableOpacity>
<TouchableOpacity
onPress={() => onTabChange(’CONFIGURATION’)}
style={[styles.tab, activeTab === ’CONFIGURATION’ && styles.activeTab]} >
<Text style={styles.tabText}> Réglages</Text>
</TouchableOpacity>
</View>
</View>
);
}

### 40 File Documentation

### 7.10.2.4 react

import React from react

### 7.10.2.5 styles

const styles

### 7.10.2.6 TabHeader

export default TabHeader

@function TabHeader

Barre d’onglets principale

Parameters

{TabHeaderProps} props - Propriétés du composant

Returns

{React.JSX.Element} En-tête avec trois onglets

## 7.11 mobile/components/ui/AppButton.tsx File Reference

Bouton applicatif stylé (primaire, danger, outline) avec état de chargement.

Variables

- import React from react
- import { TouchableOpacity, Text, StyleSheet, TouchableOpacityProps, ActivityIndicator } from 'react-native'
- interface AppButtonProps extends TouchableOpacityProps
- variant __pad0__
- isLoading __pad1__
- export const AppButton

@function AppButton
- export const variant = 'primary'
- export const isLoading = false
- export const style
- export const disabled
- export const props
- const styles

7.11 mobile/components/ui/AppButton.tsx File Reference | 41

### 7.11.1 Detailed Description

Bouton applicatif stylé (primaire, danger, outline) avec état de chargement.

### 7.11.2 Variable Documentation

### 7.11.2.1 __pad0__

variant __pad0__

### 7.11.2.2 __pad1__

isLoading __pad1__

### 7.11.2.3 AppButton

export const AppButton

@function AppButton

Bouton réutilisable avec variantes et état de chargement

Parameters

{AppButtonProps} props - Propriétés du composant

Returns

{React.JSX.Element} Bouton stylé

### 7.11.2.4 disabled

export const disabled

### 7.11.2.5 import

import { TouchableOpacity, Text, StyleSheet, TouchableOpacityProps, ActivityIndicator } from

'react-native'

### 7.11.2.6 isLoading

export const isLoading = false

### 42 File Documentation

### 7.11.2.7 props

export const props

### 7.11.2.8 react

import React from react

### 7.11.2.9 style

export const style

### 7.11.2.10 styles

const styles

Initial value:

= StyleSheet.create({
base: {
paddingVertical: 14,
borderRadius: 12,
alignItems: ’center’,
justifyContent: ’center’,
shadowColor: ’#000’,
shadowOffset: { width: 0, height: 2 }, shadowOpacity: 0.1,
shadowRadius: 3,
elevation: 2,
},
text: {
fontWeight: ’700’,
fontSize: 16,
letterSpacing: 0.5,
},
disabled: {
opacity: 0.6,
}
})

### 7.11.2.11 TouchableOpacityProps

interface AppButtonProps extends TouchableOpacityProps

Initial value:

{
title: string

### 7.11.2.12 variant

export const variant = 'primary'

## 7.12 mobile/components/ui/AppInput.tsx File Reference

Champ de saisie stylé avec placeholder grisé

7.12 mobile/components/ui/AppInput.tsx File Reference | 43

Variables

- import React from react
- import { TextInput, StyleSheet, TextInputProps } from 'react-native'
- interface AppInputProps extends TextInputProps
- const styles

### 7.12.1 Detailed Description

Champ de saisie stylé avec placeholder grisé

### 7.12.2 Variable Documentation

### 7.12.2.1 import

import { TextInput, StyleSheet, TextInputProps } from 'react-native'

### 7.12.2.2 react

import React from react

### 7.12.2.3 styles

const styles

Initial value:

= StyleSheet.create({
input: {
borderWidth: 1,
borderColor: ’#E0E0E0’,
borderRadius: 12,
paddingVertical: 14,
paddingHorizontal: 16,
marginBottom: 15,
fontSize: 16,
backgroundColor: ’#F9FAFB’, color: ’#1F2937’,
},
})

### 7.12.2.4 TextInputProps

interface AppInputProps extends TextInputProps

Initial value:

{}

export const AppInput: React.FC<AppInputProps> = ({ style, ...props }) => { return (
<TextInput
style={[styles.input, style]}
placeholderTextColor="#9CA3AF" {...props}
/>
);
}

### 44 File Documentation

## 7.13 mobile/components/ui/Card.tsx File Reference

Conteneur carte avec ombre et arrondis.

Variables

- import React from react
- import { View, StyleSheet, ViewStyle, ViewProps } from 'react-native'
- interface CardProps extends ViewProps
- style __pad0__
- export const Card

@function Card
- export const style
- export const props
- const styles

### 7.13.1 Detailed Description

Conteneur carte avec ombre et arrondis.

### 7.13.2 Variable Documentation

### 7.13.2.1 __pad0__

style __pad0__

### 7.13.2.2 Card

export const Card

@function Card

Conteneur stylé type carte

Parameters

{CardProps} props - Propriétés du composant

Returns

{React.JSX.Element} Carte

### 7.13.2.3 import

import { View, StyleSheet, ViewStyle, ViewProps } from 'react-native'

7.14 mobile/hooks/useBLE.ts File Reference | 45

### 7.13.2.4 props

export const props

Initial value:

=> {
return <View style={[styles.card, style]} {...props}>{children}</View>; }

### 7.13.2.5 react

import React from react

### 7.13.2.6 style

export const style

### 7.13.2.7 styles

const styles

Initial value:

= StyleSheet.create({
card: {
backgroundColor: ’white’,
padding: 24,
borderRadius: 16,
marginBottom: 20,
shadowColor: ’#000’,
shadowOffset: { width: 0, height: 2 }, shadowOpacity: 0.1,
shadowRadius: 4,
elevation: 4,
},
})

### 7.13.2.8 ViewProps

interface CardProps extends ViewProps

Initial value:

{
children: React.ReactNode

## 7.14 mobile/hooks/useBLE.ts File Reference

Hook React pour la communication Bluetooth avec l'ESP32.

### 46 File Documentation

Variables

- import { useState, useEffect } from 'react'
- const SERVICE_UUID = "4fafc201-1fb5-459e-8fcc-c5c9c331914b"

@constant {string} SERVICE_UUID
- const CHAR_UUID = "beb5483e-36e1-4688-b7f5-ea07361b26a8"

@constant {string} CHAR_UUID
- const CHAR_IP_UUID = "12345678-1234-1234-1234-1234567890ab"

@constant {string} CHAR_IP_UUID
- const bleManager = new BleManager()

@constant {BleManager} bleManager
- export const useBLE

@function useBLE

### 7.14.1 Detailed Description

Hook React pour la communication Bluetooth avec l'ESP32.

Gère le scan BLE, la connexion à l'ESP32, et l'échange de données

### 7.14.2 Variable Documentation

### 7.14.2.1 bleManager

const bleManager = new BleManager()

@constant {BleManager} bleManager

Instance globale du gestionnaire BLE

### 7.14.2.2 CHAR_IP_UUID

const CHAR_IP_UUID = "12345678-1234-1234-1234-1234567890ab"

@constant {string} CHAR_IP_UUID

UUID de la caractéristique BLE pour lire l'adresse IP de l'appareil

### 7.14.2.3 CHAR_UUID

const CHAR_UUID = "beb5483e-36e1-4688-b7f5-ea07361b26a8"

@constant {string} CHAR_UUID

UUID de la caractéristique BLE pour la configuration WiFi et localisation

7.15 mobile/hooks/useWindowApi.ts File Reference | 47

### 7.14.2.4 import

import { useState, useEffect } from 'react'

### 7.14.2.5 SERVICE_UUID

const SERVICE_UUID = "4fafc201-1fb5-459e-8fcc-c5c9c331914b"

@constant {string} SERVICE_UUID

UUID du service BLE principal

### 7.14.2.6 useBLE

export const useBLE

@function useBLE

Hook pour gérer les opérations Bluetooth

Fournit :

- Le statut de la connexion BLE
- L'état du scan
- Une fonction pour configurer l'ESP32 via BLE
- Une fonction pour récupérer l'IP de l'ESP32 via BLE

Returns

{Object} Objet contenant les états et fonctions BLE

{string} bleStatus - Message de statut de la connexion BLE

{boolean} isScanning - Indique si un scan est en cours

{Function} scanAndConfigure - Configure l'ESP32 avec WiFi/GPS

{Function} scanAndGetIp - Récupère l'adresse IP de l'ESP32

## 7.15 mobile/hooks/useWindowApi.ts File Reference

Hook React pour communiquer avec l'API smart-vmc.

### 48 File Documentation

Variables

- import { useState, useCallback } from 'react'
- export interface WindowState
- temp __pad0__
- aqi __pad1__
- targetAngle __pad2__
- autoMode __pad3__
- safetyLockout __pad4__
- currentLoad __pad5__
- tMax __pad6__
- tMin __pad7__
- aqiMax __pad8__
- export const useWindowApi

@function useWindowApi
- const sendAngle

@function sendAngle
- const toggleAutoMode

@function toggleAutoMode
- const resetSafety

@function resetSafety
- const updateThresholds

@function updateThresholds
- return

### 7.15.1 Detailed Description

Hook React pour communiquer avec l'API smart-vmc.

Fournit les appels REST pour lire l'état et piloter la VMC (ouverture, mode auto, seuils, sécurité).

### 7.15.2 Variable Documentation

### 7.15.2.1 __pad0__

temp __pad0__

### 7.15.2.2 __pad1__

aqi __pad1__

### 7.15.2.3 __pad2__

targetAngle __pad2__

7.15 mobile/hooks/useWindowApi.ts File Reference | 49

### 7.15.2.4 __pad3__

autoMode __pad3__

### 7.15.2.5 __pad4__

safetyLockout __pad4__

### 7.15.2.6 __pad5__

currentLoad __pad5__

### 7.15.2.7 __pad6__

tMax __pad6__

### 7.15.2.8 __pad7__

tMin __pad7__

### 7.15.2.9 __pad8__

aqiMax __pad8__

### 7.15.2.10 import

import { useState, useCallback } from 'react'

### 7.15.2.11 resetSafety

const resetSafety

Initial value:

= async () => {
try {
const response = await fetch(`http:
method: ’POST’,
body: JSON.stringify({ resetSafety: true }) });
const json = await response.json();
setWindowState(json.state || json);
Alert.alert("Info", "Système réarmé. Vérifiez qu’il n’y a plus d’obstruction."); } catch (e) {
Alert.alert("Erreur", "Impossible de réarmer");
}
}

@function resetSafety

Réarme le verrouillage de sécurité

### 50 File Documentation

### 7.15.2.12 return

return

Initial value:

{
windowState,
fetchStatus,
sendCommand,
sendAngle,
toggleAutoMode,
resetSafety,
updateThresholds,
isLoading
}

### 7.15.2.13 sendAngle

const sendAngle

Initial value:

= async (angle: number) => { try {
const response = await fetch(`http: method: ’POST’,
body: JSON.stringify({ angle }) });
const json = await response.json(); setWindowState(json.state || json); } catch (e) {
console.log(e);
}
}

@function sendAngle

Positionne la fenêtre à un angle précis

Parameters

{number} angle - Angle cible (0-90)

### 7.15.2.14 toggleAutoMode

const toggleAutoMode

Initial value:

= async (value: boolean) => { try {
const response = await fetch(`http:
method: ’POST’,
body: JSON.stringify({ autoMode: value }) });
const json = await response.json(); setWindowState(json.state || json);
} catch (e) {
Alert.alert("Erreur", "Impossible de changer le mode"); }
}

@function toggleAutoMode

Active/désactive le mode automatique

Parameters

7.15 mobile/hooks/useWindowApi.ts File Reference | 51
{boolean} | value - true pour activer

### 7.15.2.15 updateThresholds

const updateThresholds
Initial value:

= async (tMax: number, tMin: number, aqiMax: number) => { setIsLoading(true);
try {
const response = await fetch(`http:
method: ’POST’,
body: JSON.stringify({ tMax, tMin, aqiMax }) });
const json = await response.json(); setWindowState(json.state || json); Alert.alert("Succès", "Paramètres sauvegardés !"); } catch (e) {
Alert.alert("Erreur", "Echec sauvegarde");
} finally {
setIsLoading(false);
}
}
@function updateThresholds

Met à jour les seuils température/AQI

Parameters

{number} | tMax - Seuil max
{number} | tMin - Seuil min
{number} | aqiMax - Seuil AQI max

### 7.15.2.16 useWindowApi

export const useWindowApi
@function useWindowApi

Hook pour appeler l'API HTTP de l'ESP32

Parameters

{string} serverIp - Adresse IP de l'ESP32 (ex: "192.168.1.50")

Returns

{object} API du hook
{WindowState|null} return.windowState - Dernier état connu

{() => Promise<void>} return.fetchStatus - Récupère l'état courant {(action:'open'|'close') => Promise<void>} return.sendCommand - Ouvre/ferme

{(angle:number) => Promise<void>} return.sendAngle - Définit un angle précis

{(value:boolean) => Promise<void>} return.toggleAutoMode - Active/désactive le mode auto

{() => Promise<void>} return.resetSafety - Réarme la sécurité

{(tMax:number,tMin:number,aqiMax:number)=>Promise<void>} return.updateThresholds - Met à jour les seuils
{boolean} return.isLoading - Indique si une requête de seuils est en cours

### 52 File Documentation

### 7.15.2.17 WindowState

export interface WindowState

Initial value:

{
isOpen: boolean

## 7.16 mobile/services/NotificationService.ts File Reference

Classes

- class NotificationService

Service pour gérer les notifications locales.

Variables

- import notifee

### 7.16.1 Variable Documentation

### 7.16.1.1 notifee

import notifee

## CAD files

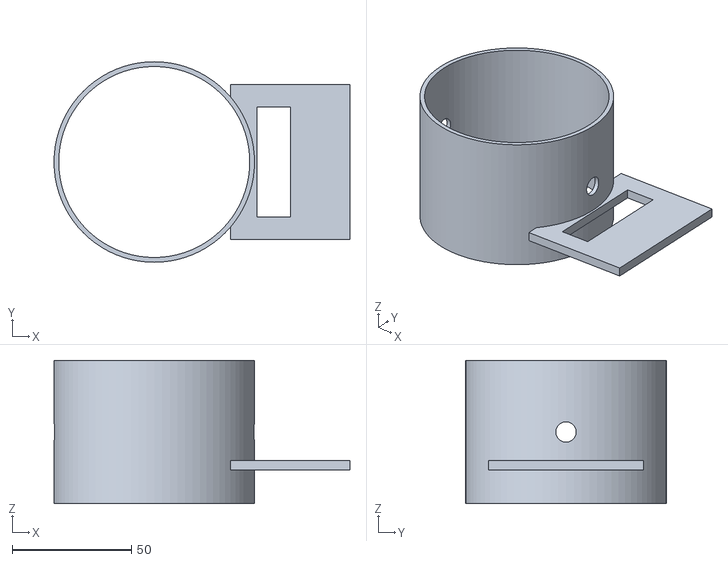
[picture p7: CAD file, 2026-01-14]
Impression3DetDecoupe/tube.stl
124.0 x 84.0 x 60.0

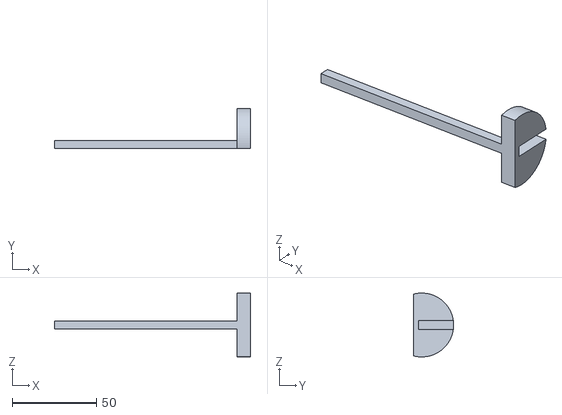
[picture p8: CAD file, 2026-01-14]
Impression3DetDecoupe/axis_motor.stl
116.5 x 24.0 x 38.0

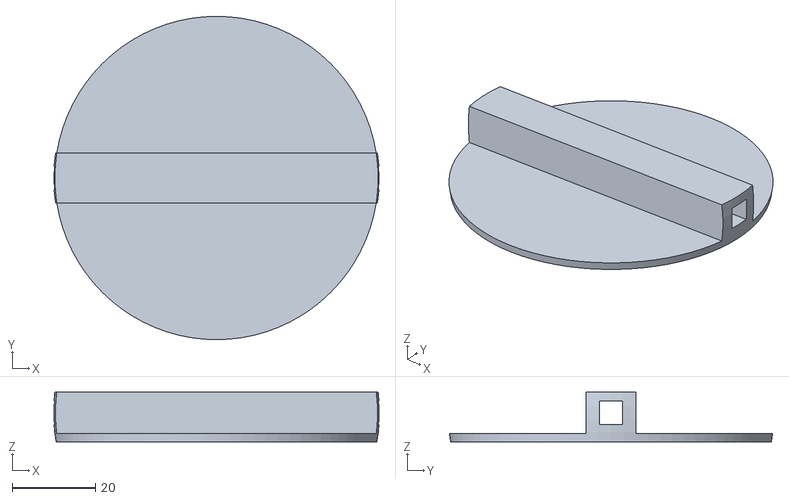
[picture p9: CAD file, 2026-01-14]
Impression3DetDecoupe/flap.stl
78.1 x 77.7 x 12.0

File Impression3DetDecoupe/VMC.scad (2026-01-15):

// --- PARAMETRES ---
vmc_diameter = 80; 
wall_thickness = 2.0;
clearance = 0.8;
angle_fente = 0; 

// Mettez "axis_motor" pour bien voir la tige hybride
part_to_show = "all"; 

// --- FIN PARAMETRES ---

$fn = 80;

outer_d = vmc_diameter + (wall_thickness * 2);
flap_d = vmc_diameter - (clearance * 2);

square_size = 5; 
hole_d = 8.5; 

pos_axe = outer_d/2 + 8;
shelf_offset = 12; 
z_offset_flap = 7;

module tube() {
    difference() {
        union() {
            cylinder(h = 60, d = outer_d, center = true);
            translate([outer_d/2 + 15, 0, -shelf_offset - 2]) 
                cube([50, 65, 4], center=true); 
        }
        cylinder(h = 65, d = vmc_diameter, center = true);
        rotate([0, 90, 0])
            cylinder(h = outer_d + 50, d = hole_d, center = true);
        translate([pos_axe, 0, -shelf_offset - 2])
            cube([14, 46, 10], center=true); 
    }
}

module flap() {
    difference() {
        union() {
            cylinder(h = 2, d = flap_d);
            translate([-flap_d/2, -6, 2])
                cube([flap_d, 12, 10]);
        }
        translate([0, 0, z_offset_flap])
            rotate([0, 90, 0])
                cube([square_size + 0.6, square_size + 0.6, flap_d + 20], center=true);
        translate([0,0,z_offset_flap]) {
            difference() {
                cylinder(h=50, d=flap_d + 20, center=true);
                sphere(d=flap_d); 
            }
        }
    }
}

module axis_insert() {
    union() {
        // 1. LA TÊTE (D)
        translate([0,0,0]) rotate([0,90,0]) {
            difference() {
                intersection() {
                     // Centré, épaisseur 5mm comme la tige
                     cylinder(h=square_size, d=38, center=true); 
                     translate([0, 15, 0]) cube([40, 40, 20], center=true);
                }
                rotate([0, 0, angle_fente])
                    translate([0, 10, 0]) cube([5.5, 24, 10], center=true);
                translate([0,0,0]) cylinder(h=20, d=2.8, center=true);
            }
        }
        
        // 2. LA TIGE HYBRIDE (Rond - Carré - Rond)
        // La tête est à X=0. Le tube commence à X = -8.
        // Diamètre intérieur du tube = 80mm.
        
        // A. PREMIER ROND (Côté Tête)
        // Il doit traverser l'espace vide (8mm) + le mur (2mm) + un peu de marge
        // Position : part de la tête (X=0) et va vers la gauche
        translate([-8, 0, 0]) 
            rotate([0, 90, 0])
            cylinder(h=16, d=square_size, center=true);

        // B. LE CARRÉ (Au milieu)
        // Il doit être DANS le tube pour entrainer le clapet.
        // Le tube fait 80mm de large à l'intérieur.
        // On fait un carré de 75mm pour être sûr d'être dedans sans toucher les murs ronds
        translate([-(outer_d/2 + 8), 0, 0]) // Centré sur le tube
            cube([70, square_size, square_size], center=true);

        // C. DEUXIÈME ROND (Côté Opposé)
        // Il traverse l'autre mur
        translate([-(outer_d + 12), 0, 0]) 
            rotate([0, 90, 0])
            cylinder(h=16, d=square_size, center=true);
    }
}

// --- AFFICHAGE ---

if (part_to_show == "tube") tube();
if (part_to_show == "flap") flap();

if (part_to_show == "axis_motor") {
    rotate([0, -90, 0]) axis_insert();
}

if (part_to_show == "all") {
    union() {
        color("LightGrey") tube();
        color("Red") translate([0, 0, -z_offset_flap]) flap(); 
        color("Cyan") translate([pos_axe, 0, 0]) axis_insert();
    }
}

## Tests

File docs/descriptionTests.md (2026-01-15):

# Documentation des Tests - Smart VMC

Ce document décrit la stratégie de test pour valider le fonctionnement de la Smart VMC (Firmware ESP32 + Application Mobile).

## Vue d'ensemble

Nous utilisons 3 niveaux de tests :
1.  **Tests Unitaires Firmware (C++)** : Valident les règles de décision (Météo -> Ouverture) sans modifier le code principal.
2.  **Tests Unitaires Mobile (Jest)** : Valident l'affichage et les composants de l'application React Native.
3.  **Tests d'Intégration (Script & Manuel)** : Valident la communication réelle entre l'App et l'ESP32.

---

## 1. Tests Unitaires Firmware (Logique)

Ces tests vérifient que l'algorithme de décision (Seuils Température/Pollution) fonctionne correctement. Ils utilisent une approche "Shadow Testing" (copie de la logique dans le test) pour ne pas avoir à modifier la structure du `main.cpp`.

* **Fichier de test** : `firmware/test/test_logic_rules.cpp`
* **Outil** : PlatformIO / Unity

### Comment lancer les tests ?

1.  Connectez votre ESP32 à l'ordinateur via USB.
2.  Ouvrez un terminal dans le dossier `firmware/` (ou utilisez le terminal PlatformIO dans VSCode).
3.  Exécutez la commande :

```bash
pio test -e esp32dev
```

### Résultats attendus
Vous devriez voir une série de succès (PASSED) correspondant aux scénarios :
* `test_cas_nominal_ouverture`
* `test_protection_chaleur`
* `test_protection_pollution`
* `test_conservation_chaleur`

---

## 2. Tests Unitaires Mobile (Interface)

Ces tests vérifient que l'interface utilisateur réagit correctement aux données (affichage des alertes, changement de couleur, etc.).

* **Dossier de tests** : `mobile/__tests__/`
* **Outil** : Jest (inclus dans React Native)

### Comment lancer les tests ?

1.  Ouvrez un terminal dans le dossier `mobile/`.
2.  Exécutez la commande :

```bash
npm test
```

### Ce qui est testé
* **StatusDisplay** : Vérifie que le sens interdit rouge s'affiche en cas de sécurité active.
* **SensorRow** : Vérifie l'affichage correct des températures et AQI.
* **ControlPanel** : Vérifie que les boutons de contrôle manuel sont désactivés/remplacés en cas d'urgence.

---

## 3. Tests d'Intégration (Robot Testeur)

Ce script automatique ("Robot") se comporte comme une application mobile. Il envoie des ordres à l'ESP32 via le réseau WiFi et vérifie que l'ESP32 obéit.

* **Fichier de script** : `scripts/test-api.js`
* **Pré-requis** : Node.js installé.

### Comment lancer le test ?

1.  Assurez-vous que l'ESP32 est allumé et connecté au même réseau WiFi que votre ordinateur.
2.  Récupérez son **adresse IP** (via le Moniteur Série ou l'écran de l'application).
3.  À la racine du projet, lancez :

```bash
node scripts/test-api.js <IP_DE_VOTRE_ESP32>
```
*Exemple : `node scripts/test-api.js 192.168.1.45`*

### Scénario exécuté
Le script va automatiquement :
1.  Vérifier la connexion (Ping/Status).
2.  Forcer le mode manuel et ouvrir la trappe.
3.  Vérifier que la trappe est bien à 90°.
4.  Fermer la trappe et vérifier le retour à 0°.
5.  Réactiver le mode automatique.
6.  **(Interactif)** Vous demander de déclencher la sécurité manuellement pour valider l'arrêt d'urgence.

---

## 4. Validation Manuelle (Cahier de Recette)

Pour les tests physiques impliquant le matériel (Moteur, Capteur de courant), référez-vous au document de validation manuelle.

### Test Critique : Sécurité Hardware
Pour valider l'exigence 07 sans endommager le moteur :
1.  Lancer le système.
2.  Utiliser un fil (jumper) pour relier brièvement le **PIN 34** au **3.3V**.
3.  **Résultat immédiat attendu** :
    * Arrêt du moteur (si en mouvement).
    * Apparition de l'écran "SÉCURITÉ ACTIVE" sur l'application mobile.
    * Verrouillage des commandes jusqu'au clic sur "DÉBLOQUER".

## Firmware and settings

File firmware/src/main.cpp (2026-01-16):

#include <main.hpp>

Servo windowServo;
Preferences preferences;
WebServer server(3001);

BLECharacteristic *pIpChar;

String wifi_ssid = "";
String wifi_pass = "";

// Grenoble
float latitude = 45.18;
float longitude = 5.72;

float tempMax = 30.0;
float tempMin = 18.0;
int aqiMax = 50;

bool isOpen = false;
bool autoMode = true;
int targetAngle = 0;

bool safetyLockout = false;
int lastCurrentReading = 0;

float lastTemp = 0.0;
int lastAQI = 0;
unsigned long lastWeatherCheck = 0;

int currentAngle = -1;

bool shouldRestart = false;

// Vérifie l'état de la VMC (surtension/surchauffe)
bool checkSafety() {
    int sensorValue = analogRead(CURRENT_SENSOR_PIN);
    lastCurrentReading = sensorValue;

    if (sensorValue > MAX_CURRENT_THRESHOLD) {
        Serial.printf("Surintensité détectée (%d). Arrêt.\n", sensorValue);
        return false;
    }
    return true;
}

// Change l'ouverture de la ventilation
void setVMC(int angle) {
    if (safetyLockout) return;

    if (!checkSafety()) {
        safetyLockout = true;
        windowServo.detach();
        return;
    }

    if (angle < 0) angle = 0;
    if (angle > 90) angle = 90;
    
    if (currentAngle == angle) return;

    if (!windowServo.attached()) {
        windowServo.attach(SERVO_PIN);
    }

    windowServo.write(angle);
    currentAngle = angle;
    isOpen = (angle > 0);
}

// Récupère le statut de la ventilation
void handleStatus() {
    server.sendHeader("Access-Control-Allow-Origin", "*");
    
    JsonDocument doc;
    doc["isOpen"] = isOpen;
    doc["temp"] = lastTemp;
    doc["aqi"] = lastAQI;
    doc["targetAngle"] = targetAngle;
    doc["autoMode"] = autoMode;
    
    doc["safetyLockout"] = safetyLockout;
    doc["currentLoad"] = lastCurrentReading;
    
    doc["tMax"] = tempMax; 
    doc["tMin"] = tempMin; 
    doc["aqiMax"] = aqiMax; 
    
    String response;
    serializeJson(doc, response);
    server.send(200, "application/json", response);
}

void handleControl() {
    server.sendHeader("Access-Control-Allow-Origin", "*");
    
    if (server.method() == HTTP_OPTIONS) {
        server.sendHeader("Access-Control-Allow-Methods", "POST, GET, OPTIONS");
        server.sendHeader("Access-Control-Allow-Headers", "Content-Type");
        server.send(204);
        return;
    }

    if (!server.hasArg("plain")) {
        server.send(400, "application/json", "{\"error\":\"Body missing\"}");
        return;
    }

    String body = server.arg("plain");
    JsonDocument doc;
    DeserializationError error = deserializeJson(doc, body);

    if (error) {
        server.send(400, "application/json", "{\"error\":\"Invalid JSON\"}");
        return;
    }
    
    bool thresholdsUpdated = false;

    if (doc.containsKey("resetSafety") && doc["resetSafety"] == true) {
        safetyLockout = false;
        if (!checkSafety()) {
            safetyLockout = true;
        }
    }

    if (doc.containsKey("autoMode")) {
        autoMode = doc["autoMode"];
    }
    
    if (!safetyLockout) {
        if (doc.containsKey("angle")) {
            autoMode = false;
            targetAngle = doc["angle"];
            setVMC(targetAngle);
        } 
        else if (doc.containsKey("action")) {
            autoMode = false;
            String action = doc["action"];
            if (action == "open") targetAngle = 90;
            if (action == "close") targetAngle = 0;
            setVMC(targetAngle);
        }
    }
    
    preferences.begin("config", false);

    if (doc.containsKey("tMax")) {
        tempMax = doc["tMax"].as<float>();
        preferences.putFloat("tmax", tempMax);
        thresholdsUpdated = true;
    }
    if (doc.containsKey("tMin")) {
        tempMin = doc["tMin"].as<float>();
        preferences.putFloat("tmin", tempMin);
        thresholdsUpdated = true;
    }
    if (doc.containsKey("aqiMax")) {
        aqiMax = doc["aqiMax"].as<int>();
        preferences.putInt("aqmax", aqiMax);
        thresholdsUpdated = true;
    }

    preferences.end();
    
    if (thresholdsUpdated && autoMode) {
        lastWeatherCheck = 0;
    }

    JsonDocument resDoc;
    resDoc["success"] = true;
    
    JsonObject state = resDoc.createNestedObject("state");
    state["isOpen"] = isOpen;
    state["temp"] = lastTemp;
    state["aqi"] = lastAQI;
    state["targetAngle"] = targetAngle;
    state["autoMode"] = autoMode;
    state["safetyLockout"] = safetyLockout;
    state["tMax"] = tempMax; 
    state["tMin"] = tempMin; 
    state["aqiMax"] = aqiMax; 

    String response;
    serializeJson(resDoc, response);
    server.send(200, "application/json", response);
}

class ConfigCallbacks : public BLECharacteristicCallbacks {
    void onWrite(BLECharacteristic *pCharacteristic) {
        std::string value = pCharacteristic->getValue();
        if (value.length() > 0) {
            String data = String(value.c_str());
            int s1 = data.indexOf(';');
            int s2 = data.indexOf(';', s1 + 1);
            int s3 = data.indexOf(';', s2 + 1);
            
            if (s3 > 0) {
                wifi_ssid = data.substring(0, s1);
                wifi_pass = data.substring(s1 + 1, s2);
                latitude = data.substring(s2 + 1, s3).toFloat();
                longitude = data.substring(s3 + 1).toFloat();
                
                preferences.begin("config", false);
                preferences.putString("ssid", wifi_ssid);
                preferences.putString("pass", wifi_pass);
                preferences.putFloat("lat", latitude);
                preferences.putFloat("lon", longitude);
                
                preferences.end();
                Serial.println("Configuration reçue via BLE. Redémarrage imminent...");
                shouldRestart = true;
            }
        }
    }
};

// Initialisation de la connexion
void setup() {
    Serial.begin(115200);
    windowServo.setPeriodHertz(50);
    windowServo.attach(SERVO_PIN, 500, 2400);

    preferences.begin("config", true);
    wifi_ssid = preferences.getString("ssid", "");
    wifi_pass = preferences.getString("pass", "");
    latitude = preferences.getFloat("lat", 45.18);
    longitude = preferences.getFloat("lon", 5.72);
    tempMax = preferences.getFloat("tmax", 30.0);
    tempMin = preferences.getFloat("tmin", 18.0);
    aqiMax = preferences.getInt("aqmax", 50);
    preferences.end();

    if (wifi_ssid != "") {
        WiFi.begin(wifi_ssid.c_str(), wifi_pass.c_str());
        Serial.print("Connexion WiFi...");
        int tries = 0;
        while (WiFi.status() != WL_CONNECTED && tries < 30) {
            delay(500); 
            Serial.print("."); 
            tries++;
        }
        if (WiFi.status() == WL_CONNECTED) {
            Serial.println("\n✅ WiFi Connecté ! IP: " + WiFi.localIP().toString());
            
            server.on("/api/window/status", HTTP_GET, handleStatus);
            server.on("/api/window/control", HTTP_POST, handleControl);
            server.onNotFound([]() { server.send(404, "text/plain", "Not Found"); });
            server.begin();
        } else {
            Serial.println("\n❌ Échec WiFi");
        }
    }

    BLEDevice::init("ESP32_SmartWindow");
    BLEServer *pServer = BLEDevice::createServer();
    BLEService *pService = pServer->createService(SERVICE_UUID);
    
    BLECharacteristic *pChar = pService->createCharacteristic(CHAR_CONFIG_UUID, NIMBLE_PROPERTY::READ | NIMBLE_PROPERTY::WRITE);
    pChar->setCallbacks(new ConfigCallbacks());
    
    pIpChar = pService->createCharacteristic(CHAR_IP_UUID, NIMBLE_PROPERTY::READ);
    
    String currentIp = (WiFi.status() == WL_CONNECTED) ? WiFi.localIP().toString() : "0.0.0.0";
    pIpChar->setValue(std::string(currentIp.c_str())); 

    pService->start();
    BLEDevice::getAdvertising()->addServiceUUID(SERVICE_UUID);
    BLEDevice::getAdvertising()->start();
}

// Boucle d'exécution principale
void loop() {
    if (shouldRestart)
    {
        delay(1000);
        ESP.restart();
    }
    if (WiFi.status() == WL_CONNECTED) {
        server.handleClient();
    }

    if (millis() - lastWeatherCheck > 60000 || lastWeatherCheck == 0) {
        if (WiFi.status() == WL_CONNECTED) {
            HTTPClient http;
            http.begin("https://api.open-meteo.com/v1/forecast?latitude=" + String(latitude) + "&longitude=" + String(longitude) + "&current=temperature_2m,european_aqi");
            int code = http.GET();
            if (code > 0) {
                String payload = http.getString();
                JsonDocument doc; deserializeJson(doc, payload);
                lastTemp = doc["current"]["temperature_2m"];
                lastAQI = doc["current"]["european_aqi"];
                Serial.println("🌡 Température: " + String(lastTemp) + " °C, AQI: " + String(lastAQI));
                if (doc["current"]["european_aqi"].isNull()) lastAQI = 20;
                
                if (autoMode && !safetyLockout) {
                    if (lastTemp > tempMax || lastAQI > aqiMax)
                    {
                        targetAngle = 0;
                        setVMC(0);
                        Serial.println("Fermeture");
                    }
                    else if (lastTemp > tempMin) {
                        targetAngle = 90;
                        setVMC(90);
                        Serial.println("Ouverture");
                    }
                    else {
                        targetAngle = 0;
                        setVMC(0);
                        Serial.println("Fermeture");
                    }
                }
            }
            http.end();
        }
        lastWeatherCheck = millis();
    }
    delay(5);
}

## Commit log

2025-12-16 Fix IP address typo
    [main.cpp]
2025-12-16 Remove backend and host server on ESP32
2025-12-16 New page for temp and AQI configuration. Fix open/close algorithm
    [main.cpp]
2025-12-17 Fix IP Detection issue and crash when configure Wifi
    [main.cpp]
2026-01-14 Upload ImpressionFile
    [axis_motor.stl, flap.stl, tube.stl]
2026-01-15 Implement safety lockout for current sensor
    1/2 Partie CPP
2026-01-15 Add isLocked prop to StatusDisplay component
2026-01-15 Enhance ControlPanel with locking mechanism and reset action
    Added isLocked prop and onResetSafety action to ControlPanel. Implemented critical case handling for locked system.
2026-01-15 Add onResetSafety prop to DashboardPanel
    Added onResetSafety prop to DashboardPanel and updated related components.
2026-01-15 Add tests for ControlPanel component
    Added tests for ControlPanel component to verify button presence and functionality in different states.
2026-01-15 Create tests for SensorRow component
    Add tests for SensorRow component to validate temperature and AQI display.
2026-01-15 Add integration test script for Smart VMC API
    This script tests the integration of the Smart VMC API by checking the status, opening and closing the window, and switching between manual and auto modes.
2026-01-15 Add unit tests for decisionVMC function
    This file contains tests for the decisionVMC function, which evaluates temperature and air quality index (AQI) to determine whether to open or close a ventilation system. It includes multiple test ca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
2026-01-15 Upload .scad
    [VMC.scad]
2026-01-16 Switch to pdf doxyfile
